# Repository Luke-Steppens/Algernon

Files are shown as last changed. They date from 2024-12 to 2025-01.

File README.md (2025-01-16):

# Micromouse Project - COMP207  

## Overview  
This repository contains all the resources, code, and documentation for my Micromouse project as part of the COMP207 module at Falmouth University (Second Year).  
The goal of the project is to design, build, and program a robot capable of navigating a maze efficiently.  

---

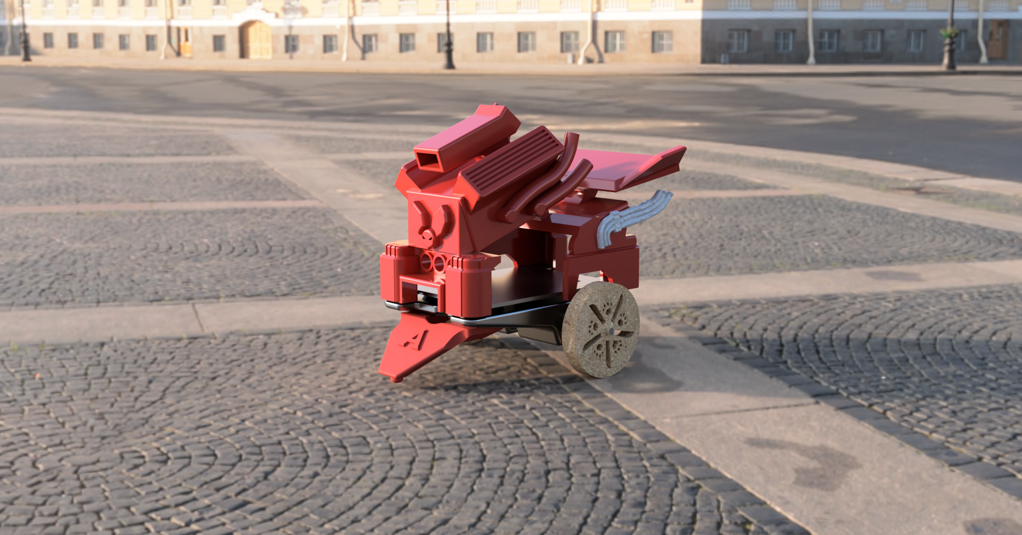
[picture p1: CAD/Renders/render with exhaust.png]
High-Resolution Render


---

## Project Goals  

1. **Design and Manufacture**  
   - Create an autonomous Micromouse capable of navigating a maze.  

2. **Documentation**  
   - Utilise tools such as:  
     - **EasyEDA**: PCB design  
     - **Fusion 360**: 3D modeling  
     - **Arduino IDE**: Programming  

3. **Practical Implementation**  
   - Use physical tools and equipment, including:  
     - 3D printers  
     - Laser cutters  
     - Soldering tools  
     - General workshop tools  

---

## Contest Rules  
For detailed guidelines on Micromouse competitions, refer to the official [Micromouse Classic Contest Rules](https://ukmars.org/contests/contest-rules/micromouse-classic/) provided by UKMARS.  

---

## Development Progress  
Track my project progress through the [COMP207 Micromouse Devlog](https://www.notion.so/COMP207-Digital-Prototyping-Logbook-7b87d9ca3a4f4ccf9538969c8f4991d4?pvs=4).  

---

## Repository Contents  
This repository is organized into the following directories:  

- **CAD**  
   - Assemblies
   - Drawings
   - Parts
   - Renders
   - Workshop Materials  

- **Code**  
   - Basic Component Code  
   - ClassCode  
   - Micro-Mouse Algernon  

- **Documentation**  
   - Screenshots & Photos
   - TCRT Test
   - Feedback Form
   - Notion

- **Electronics**
   - Datasheets

- **Media**
   - Video
   - Photo
   - Presentation - For my presentation please use this link or find the slides in this folder https://www.youtube.com/watch?v=WSdy4DRx-fY&t=1s

---

## How to Recreate the Project  

### 1. **Prepare Initial Components**  

To begin, gather the following components for the Micromouse project:  

<table>
  <tr>
    <td style="text-align: center;">
      <b>Microcontroller:</b><br>Pi Pico<br>
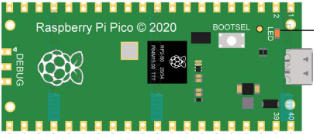
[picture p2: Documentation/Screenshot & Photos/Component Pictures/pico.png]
      
    </td>
    <td style="text-align: center;">
      <b>Motor Driver:</b><br>L293D<br>
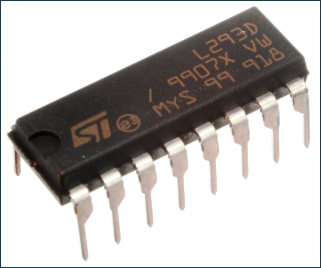
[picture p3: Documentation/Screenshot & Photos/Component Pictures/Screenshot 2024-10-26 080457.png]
      
    </td>
    <td style="text-align: center;">
      <b>Proximity Sensor:</b><br>TCRT5000<br>
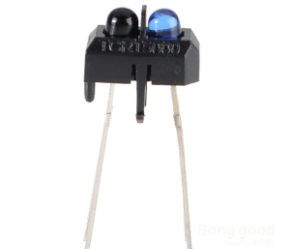
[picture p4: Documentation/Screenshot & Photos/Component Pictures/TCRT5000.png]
      
    </td>
  </tr>
  <tr>
    <td style="text-align: center;">
      <b>Voltage Regulator:</b><br>L7805<br>
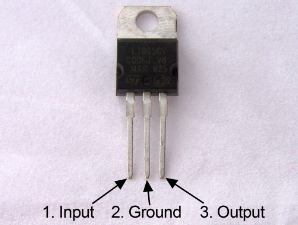
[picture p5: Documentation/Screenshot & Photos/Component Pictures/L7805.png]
      
    </td>
    <td style="text-align: center;">
      <b>Magnetometer Compass:</b><br>GY-271 HMC5883L<br>
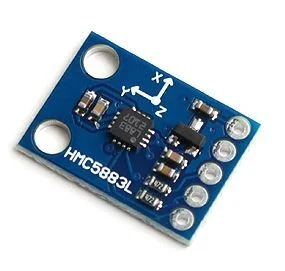
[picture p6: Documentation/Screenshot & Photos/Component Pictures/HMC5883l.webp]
      
    </td>
    <td style="text-align: center;">
      <b>DC Motors:</b><br>12V N20<br>
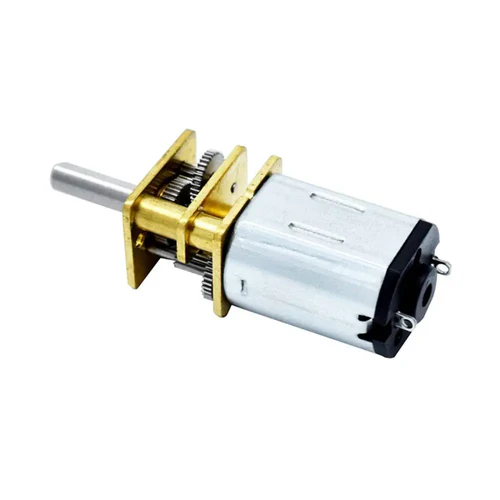
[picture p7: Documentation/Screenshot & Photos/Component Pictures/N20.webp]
      
    </td>
  </tr>
</table>
<br><br> <!-- Extra line break -->

---

### 2. **Schematic Layout - EasyEDA**  

After preparing the components, you can move on to creating the schematic in EasyEDA. This is where you arrange the components logically on the schematic to plan how they’ll be connected.  

It can often be difficult to find the item you are looking for within EasyEDA's search function, so I advise using the "User Contributed" section for additional parts.
This section has a variety of parts that other users have uploaded, which can save you time searching for specific components.

<div style="text-align: center; margin-bottom: 20px;">
  <b>User Contributed Section</b><br>
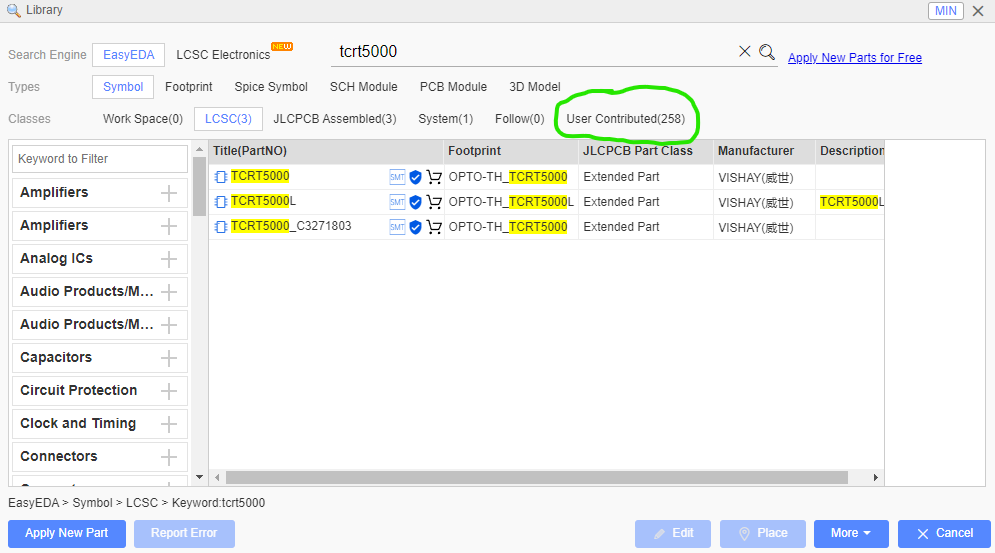
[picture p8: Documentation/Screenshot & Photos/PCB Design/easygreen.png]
  
</div>

### Component and ID’s

Here are the components used in the project along with their EasyEDA search IDs:

- **Pi Pico** - C7203003
- **Motor Driver (L293D)** - C12340
- **Proximity Sensor (TCRT5000)** - C2984661
- **Switch** - C2939728
- **Voltage Regulator (L7805)** - C347289
- **Compass (HMC5883L)** 

Here's an example of how the schematic layout in EasyEDA looks:

<div style="text-align: center; margin-bottom: 20px;">
  <b>EasyEDA Schematic Layout</b><br>
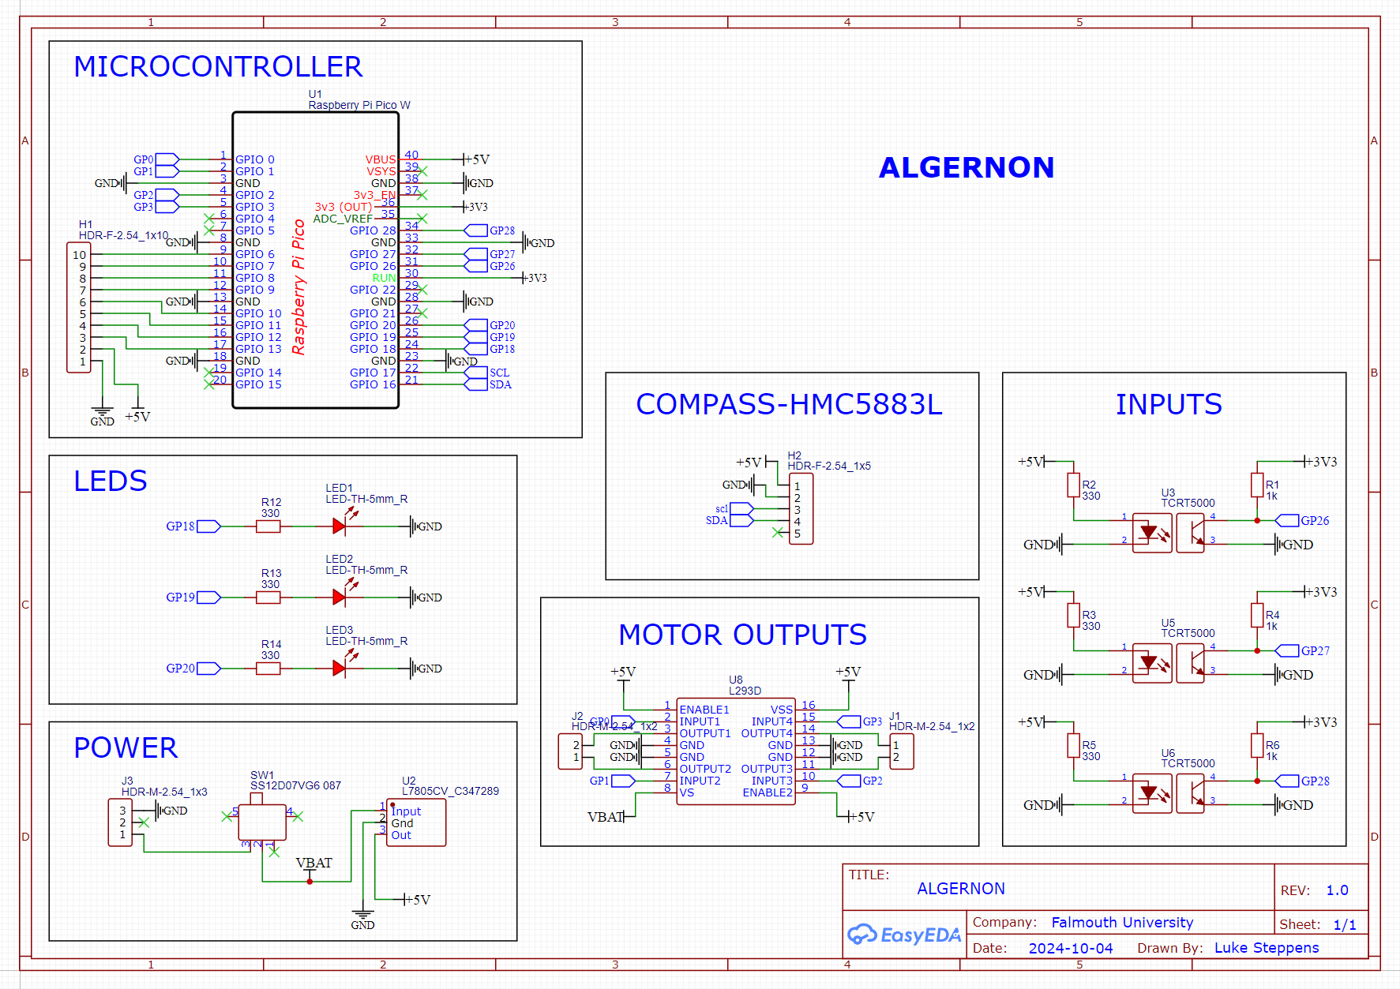
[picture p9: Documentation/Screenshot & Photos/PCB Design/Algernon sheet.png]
  
</div>
Please ensure you check your datasheets to get the connections correct. I took the incorrect details from a sellers page and had troubles down the line. (It is Corrected in this Schematic)

<br><br> <!-- Extra line break -->

---
### 3. **PCB Layout - Fusion 360 / EasyEda**

Design the base shape for your PCB in Fusion 360 by starting with a basic rectangle. Add four circles for mounting the PCB to the motor mounts,
then extrude the shape to a thickness of **1.60mm**. Apply fillets to the corners to create smooth edges. Once the base shape is complete,
create a new sketch on the surface of the design. After finishing the sketch, right-click on it in the drop-down menu and save it as a **DXF file**.

<div style="text-align: center; margin-bottom: 20px;">
  <b>Base Design of PCB</b><br>
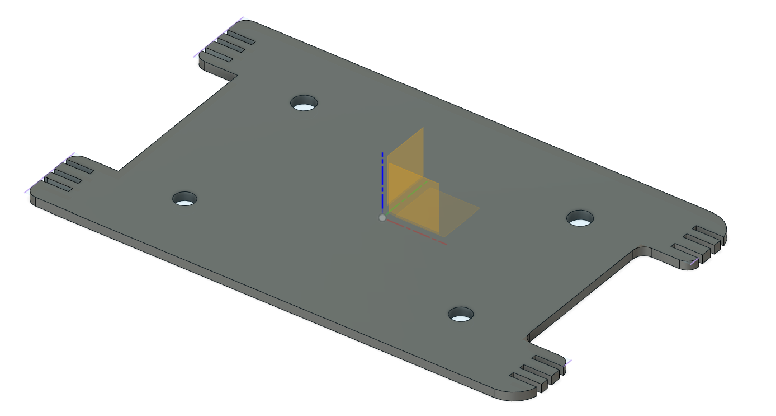
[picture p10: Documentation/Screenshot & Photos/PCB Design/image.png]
  
</div>

<br><br> <!-- Extra line break -->

The next step is to import your DXF file into EasyEDA and place your schematic on it. Consider the placement of components carefully to ensure proper functionality. For instance, the TCRT5000 proximity sensors should be positioned at the edges, and the L7805 voltage regulator is quite tall, so it may interfere with the chassis design. To make the routing process easier, we can utilize both the top and bottom layers of the PCB, represented by the red and blue lines, respectively. Add a copper layer within the PCB that way there is no need to connect ground connections, of which there are many. Alongside this do the same with +5V removing more manual connections and saving time. 
<div style="text-align: center; margin-bottom: 20px;">
  <b>Layout Considering Physicality of Components and Tracks</b><br>
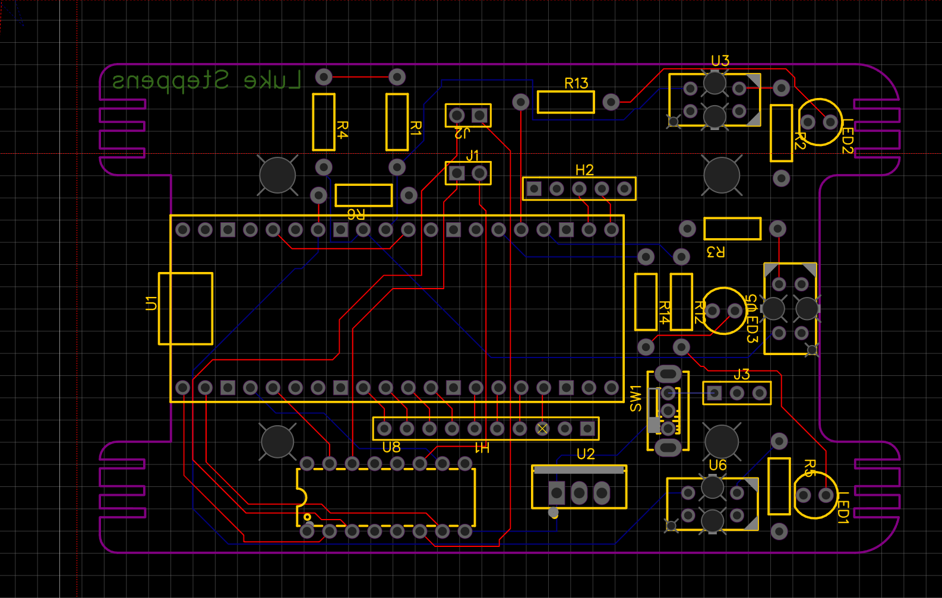
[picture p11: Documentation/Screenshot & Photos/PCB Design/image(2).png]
  
</div>

<br><br> <!-- Extra line break -->

When routing the board, avoid creating arbitrary lines. Instead, aim to have the tracks run parallel to one another. Shorter tracks result in less resistance, improving performance. Next press the Design Rule Check button too see if everything is correct, if you have no errors feel free to proceed.
<div style="text-align: center; margin-bottom: 20px;">
  <b>Final Track Layout</b><br>
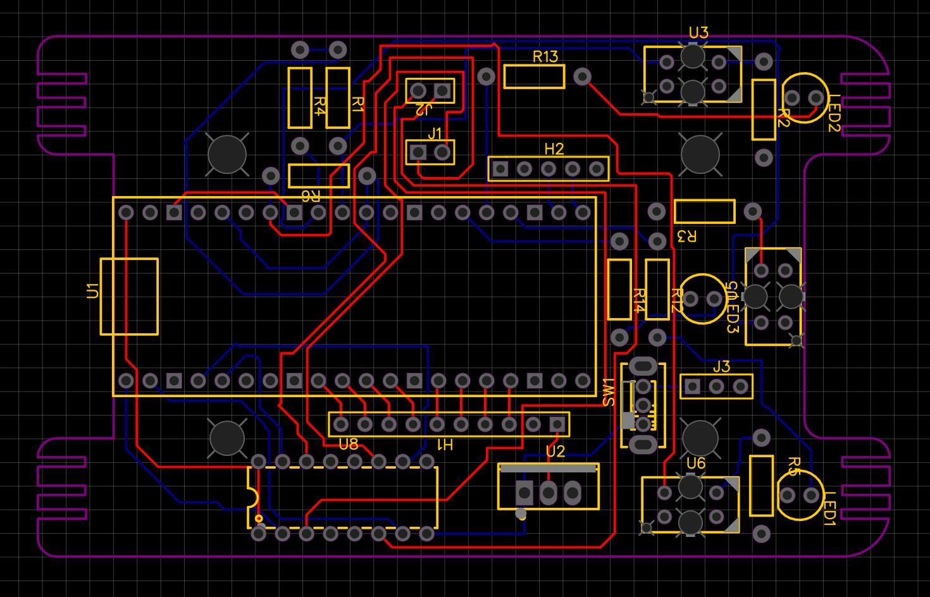
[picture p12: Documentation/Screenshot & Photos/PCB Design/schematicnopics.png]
  
</div>

<br><br> <!-- Extra line break -->

Once you are pleased with your setup press the 3D button to get an idea of the final product.
<div style="text-align: center; margin-bottom: 20px;">
  <b>PCB 3D Render</b><br>
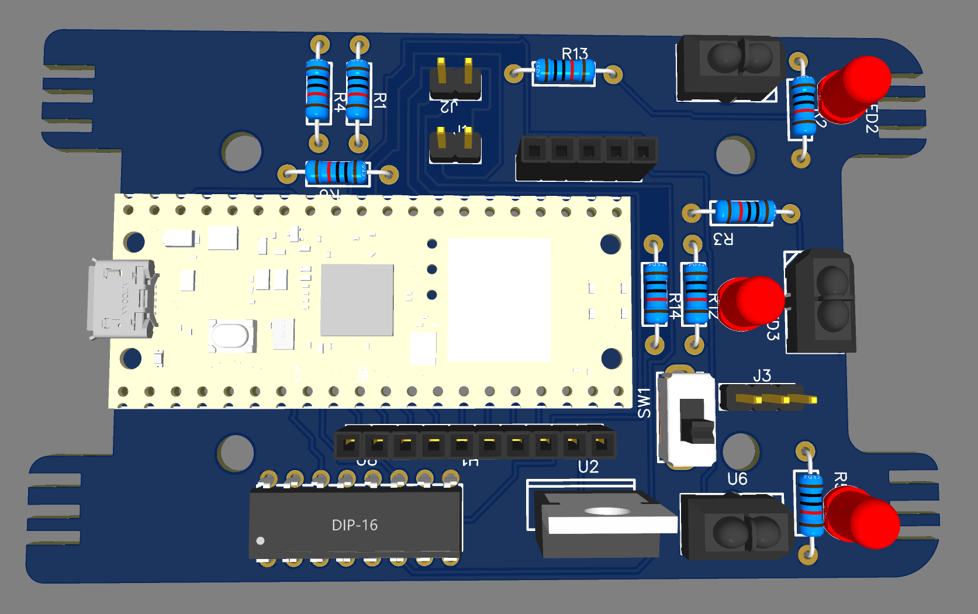
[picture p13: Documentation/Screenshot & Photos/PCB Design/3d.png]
  
</div>

---
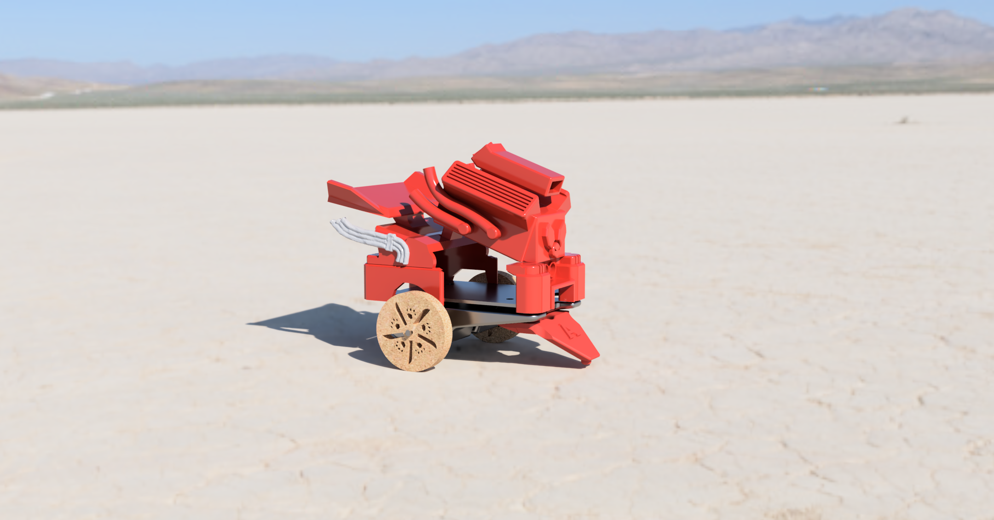
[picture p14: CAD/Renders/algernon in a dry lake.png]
High-Resolution Render


---

<br><br> <!-- Extra line break -->
---
### 4. **Motor Mounts - Fusion 360** 

Firstly a sketch is placed and we begin building a basic block with holes with which to attach the PCB. The centre rectangle was made 90mm by 25mm giving lots of space, and then use the construction line tool to find the spots 25mm away from the centre east and west. These would be the places for the PCB holes, the circle tool was used at 3.60 diameter and then use the offset tool to add another circle 2mm larger around it. Extrude 20mm leaving the two circles deselected which leaves the holes going through the block.

<div style="text-align: center; margin-bottom: 20px;">
  <b>Base Dimensions</b><br>
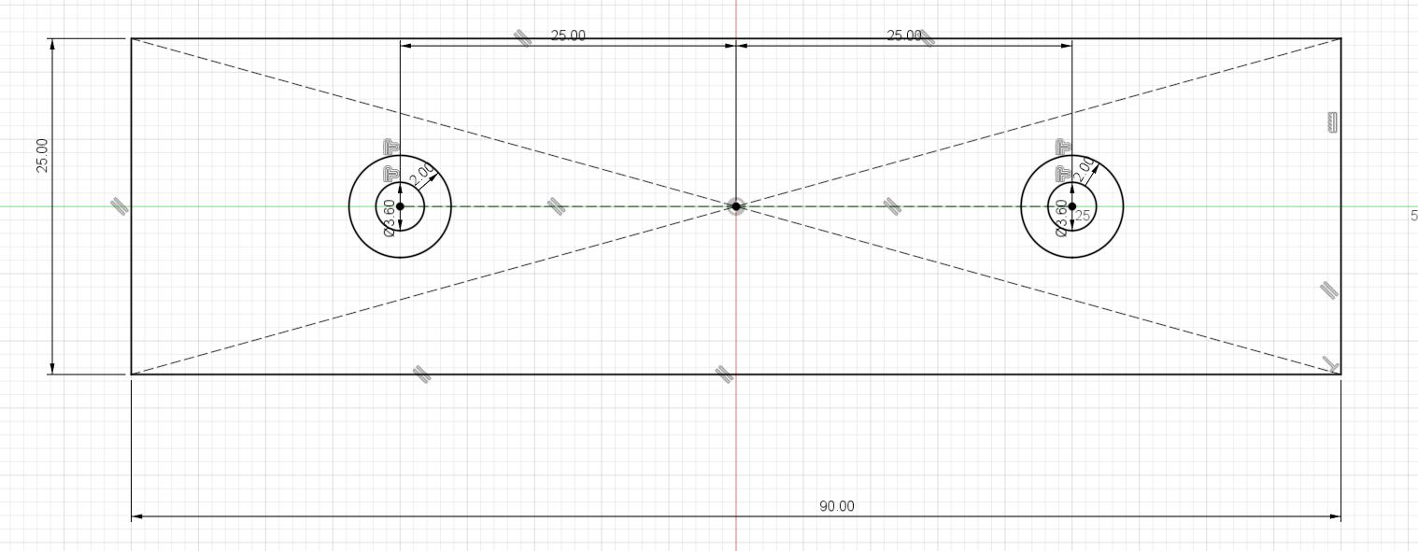
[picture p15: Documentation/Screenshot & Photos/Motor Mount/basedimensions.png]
  
</div>

<div style="text-align: center; margin-bottom: 20px;">
  <b>Base Extrude</b><br>
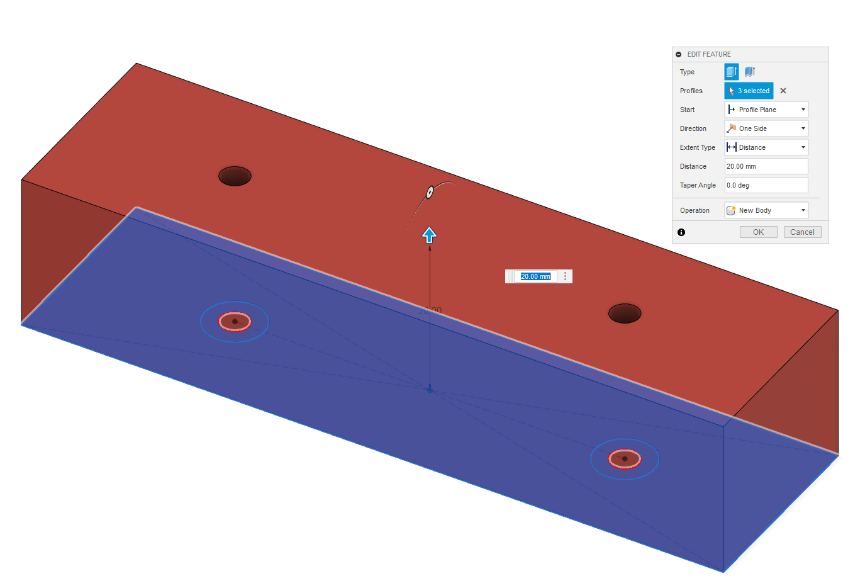
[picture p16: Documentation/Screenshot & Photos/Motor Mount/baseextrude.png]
  
</div>

<br><br> <!-- Extra line break -->

next step is to carve out the hole for the DC motor and to create the shape of the mount itself. Make a sketch on the side and then used the line tool just selecting points then extruding through. The motor hole has to follow the specification of its real life counterpart, sketch a circle of 12mm and a square of 10mm from the circles centre, this leaves the centre part ready for the extrusion process.

<table>
  <tr>
    <td style="text-align: center;">
      <b>Mount Shape</b><br>
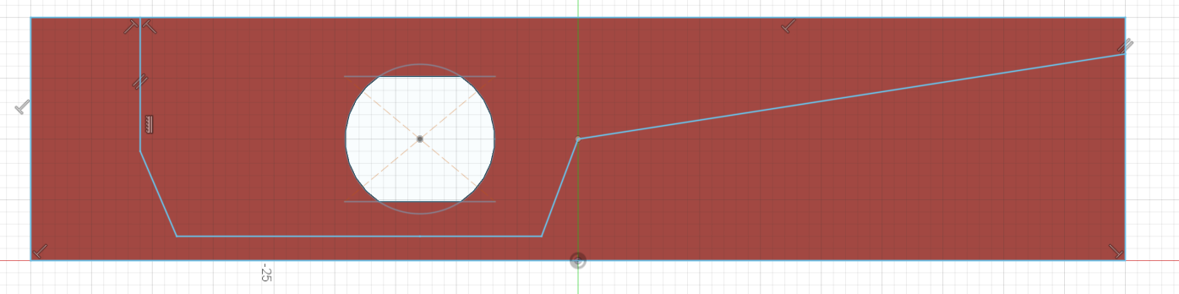
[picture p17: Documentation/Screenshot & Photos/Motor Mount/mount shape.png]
      
    </td>
    <td style="text-align: center;">
      <b>Extrude Cut</b><br>
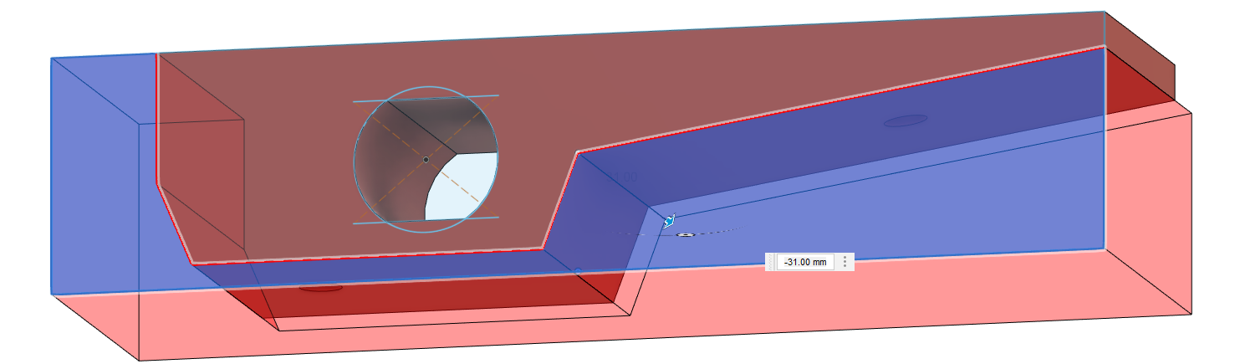
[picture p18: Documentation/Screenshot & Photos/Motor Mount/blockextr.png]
      
    </td>
  </tr>
</table>

<br><br> <!-- Extra line break -->

Between the PCB and mount we need 3mm clearance. extrude the offset circles on the surface to 3mm and then chamfer them down giving a ramped effect. Pure for aesthetics extra edges can be filleted to be smooth and rounded.

<table>
  <tr>
    <td style="text-align: center;">
      <b>Offset Circle Extrude + Offset</b><br>
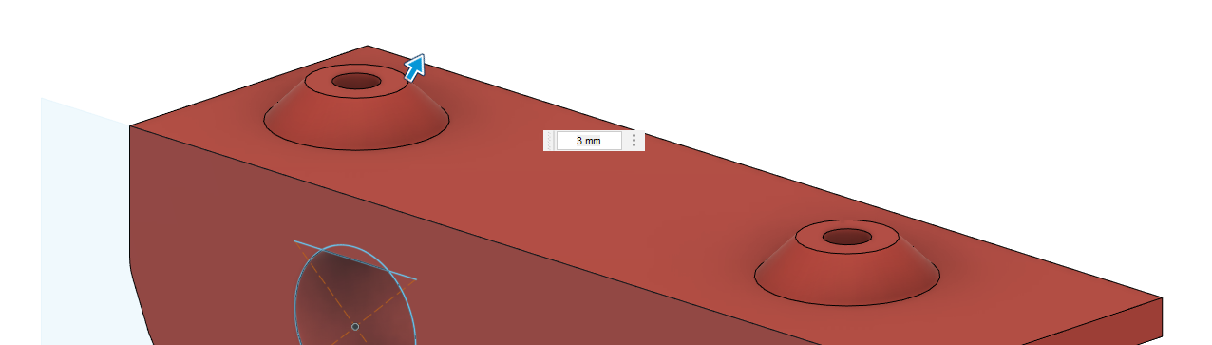
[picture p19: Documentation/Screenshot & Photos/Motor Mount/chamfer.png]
      
    </td>
    <td style="text-align: center;">
      <b>Filleted Edges</b><br>
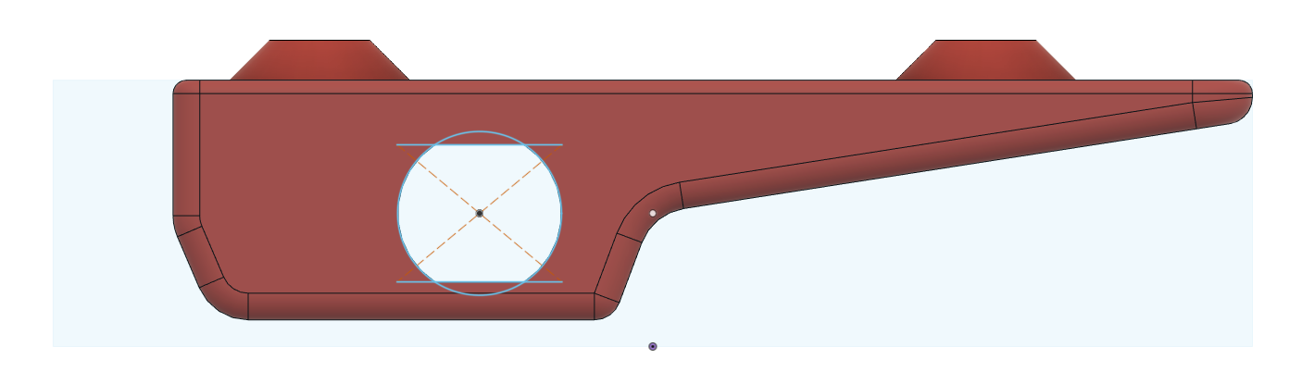
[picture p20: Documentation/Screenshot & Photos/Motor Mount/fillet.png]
      
    </td>
  </tr>
</table>
<br><br> <!-- Extra line break -->

In order to have the mount screws fit correctly a horizontal extrude is needed on the underside. An extrude was made on the side sketch of the mount with and offset creating a square within the middle. Fillet the edge, this will make attaching parts easier later on.

<div style="text-align: center; margin-bottom: 20px;">
  <b>Flat Extrude for Screw Nuts and extras</b><br>
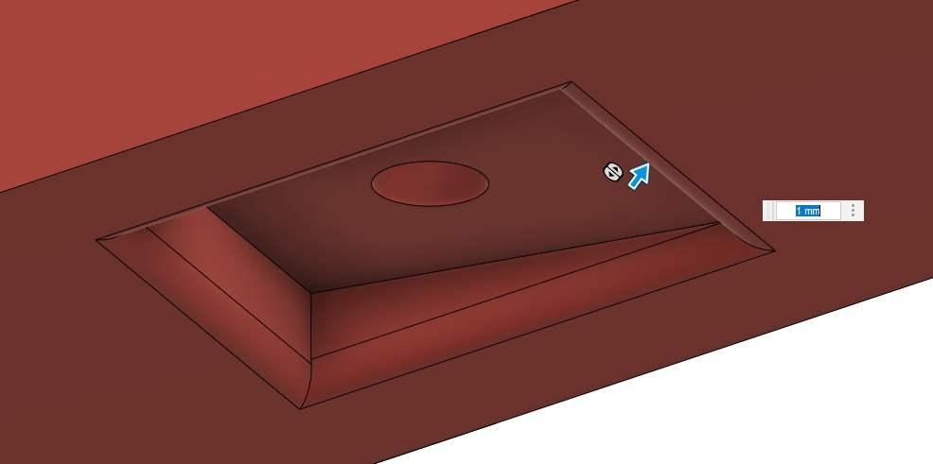
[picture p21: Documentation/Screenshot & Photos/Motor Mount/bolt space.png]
  
</div>

<br><br> <!-- Extra line break -->

For character to make the mounts match the "Paw" shape of the PCB base, cut out 12.5mm by 9mm from the edge by creating a sketch and extruding through.

<table>
  <tr>
    <td style="text-align: center;">
      <b>Paw Shape</b><br>
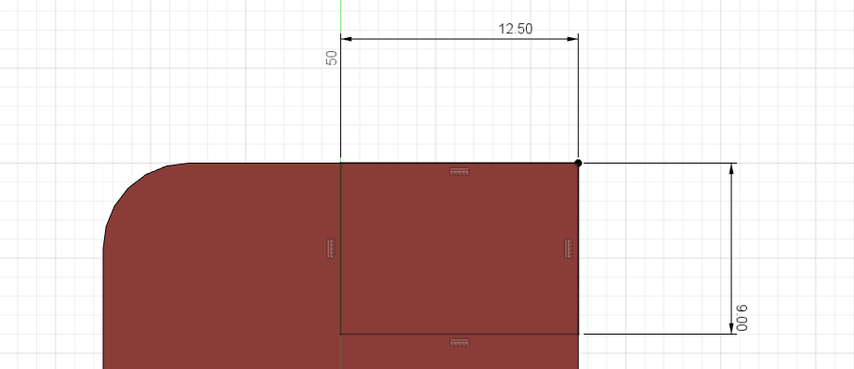
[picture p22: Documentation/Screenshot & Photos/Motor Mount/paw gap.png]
      
    </td>
    <td style="text-align: center;">
      <b>Filleted Edges</b><br>
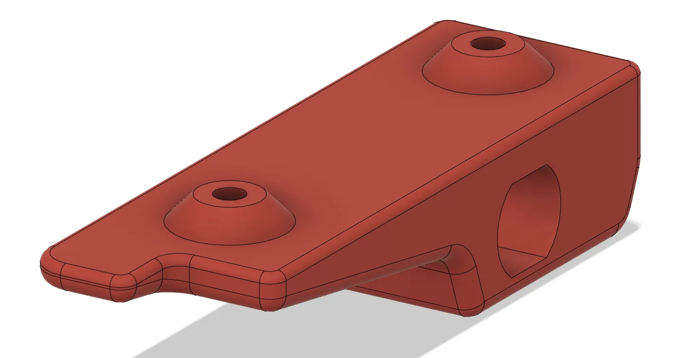
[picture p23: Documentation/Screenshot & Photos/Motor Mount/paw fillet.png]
      
    </td>
  </tr>
</table>

<br><br> <!-- Extra line break -->

To create the motor mounts counterpart create a construction plane that is offset far enough to fit the mirror image. (26mm from the side plane)

<div style="text-align: center; margin-bottom: 20px;">
  <b>Construction Plane</b><br>
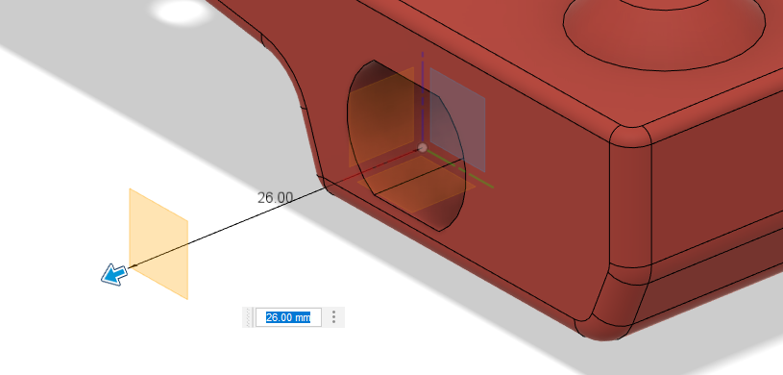
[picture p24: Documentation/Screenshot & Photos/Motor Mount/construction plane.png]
  
</div>

<div style="text-align: center; margin-bottom: 20px;">
  <b>Mirror Mount</b><br>
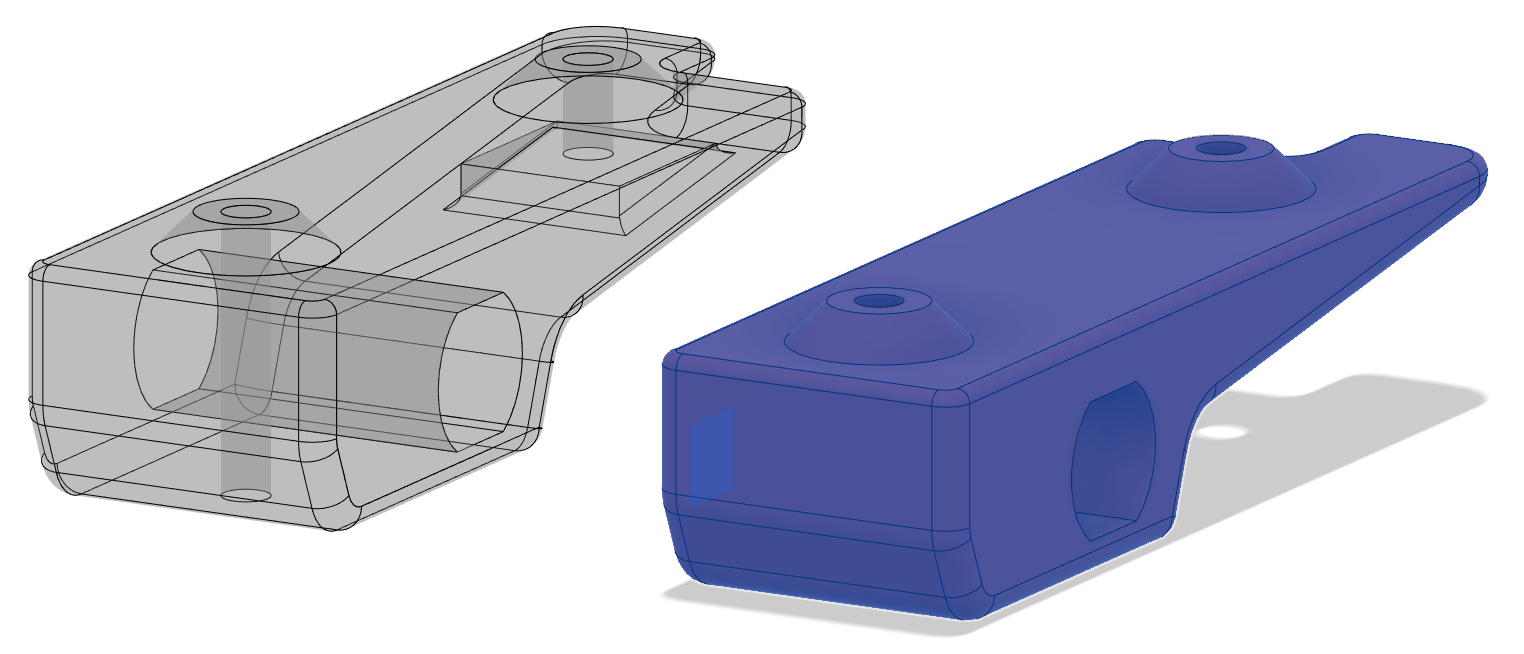
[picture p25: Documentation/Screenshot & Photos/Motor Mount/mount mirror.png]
  
</div>

<br><br> <!-- Extra line break -->

The last touch on the mounts was to add text to the them. Create sketches on the flat surfaces, choose text and type the writing. Follow this with using the alignment option to have the text centered within box. Extrude the Text by 1mm.

<table>
  <tr>
    <td style="text-align: center;">
      <b>How's My</b><br>
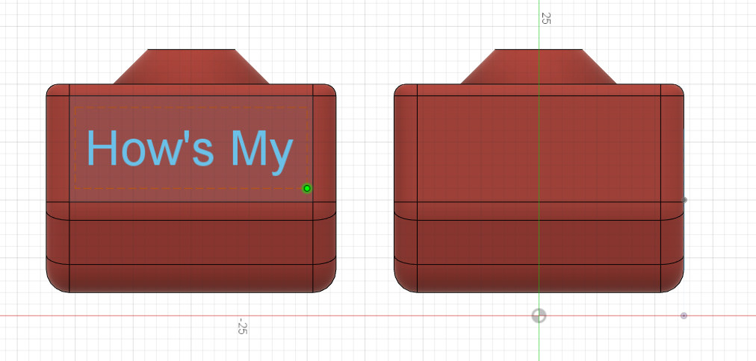
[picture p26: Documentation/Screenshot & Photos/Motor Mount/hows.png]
      
    </td>
    <td style="text-align: center;">
      <b>Driving</b><br>
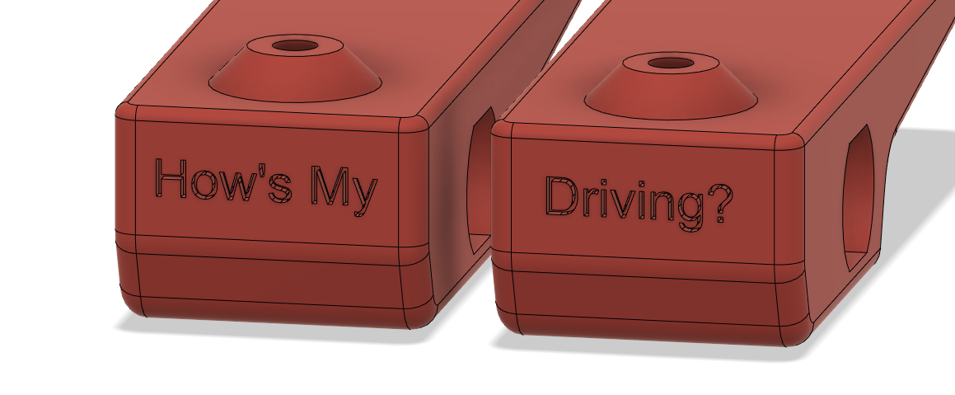
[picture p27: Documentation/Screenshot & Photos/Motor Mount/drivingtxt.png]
      
    </td>
  </tr>
</table>

<br><br> <!-- Extra line break -->

Going back into Fusion 360 you can create an assembly with all current parts which should look like this:

<div style="text-align: center; margin-bottom: 20px;">
  <b>Motor Mount + PCB Assembly </b><br>
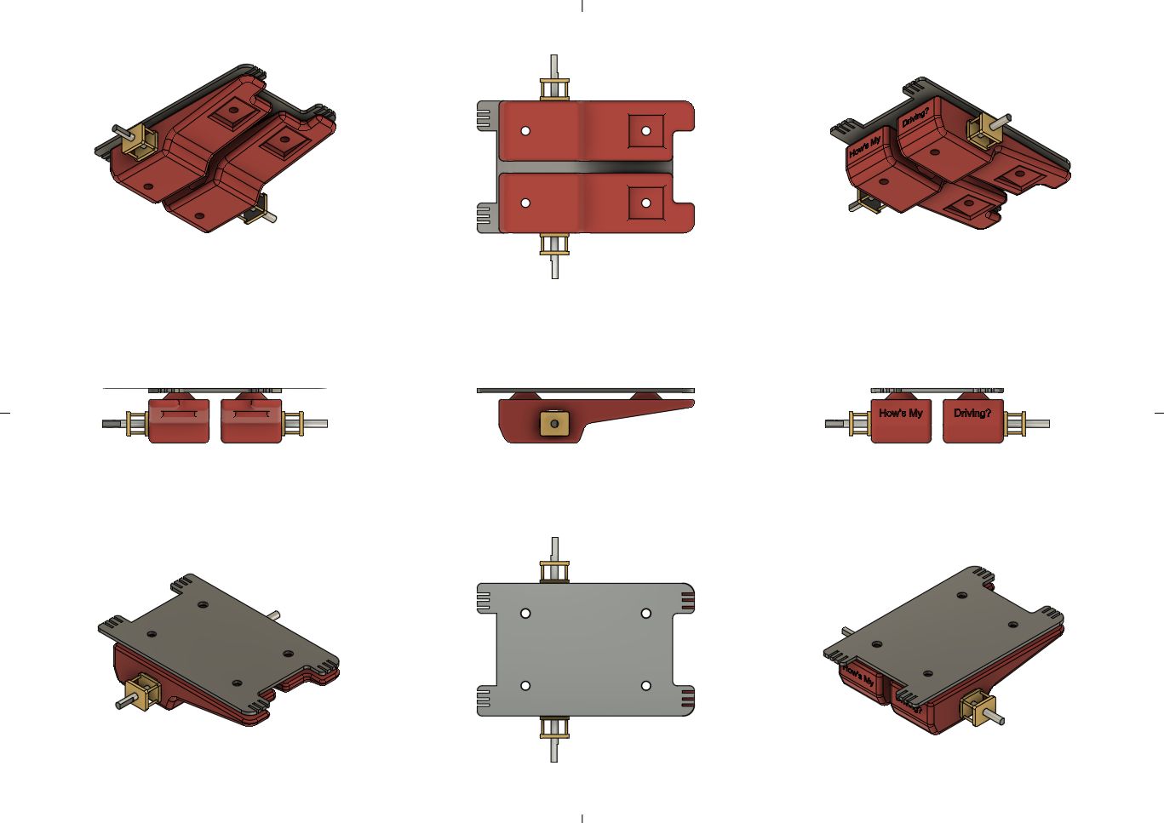
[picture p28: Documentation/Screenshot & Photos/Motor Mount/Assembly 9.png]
  
</div>

<br><br> <!-- Extra line break -->

---
### 5. **PCB Assembly & Testing - Arduino IDE**

Your PCB will need a visual inspection to ensure everything looks connected properly. Then using a multimeter go through each track end to end and connect the multimeter to the end of each tracks, if it doesnt beep they arent connected and it is ok to continue. Check every track!. 

<div style="text-align: center; margin-bottom: 20px;">
  <b>Printed Circuit Board</b><br>
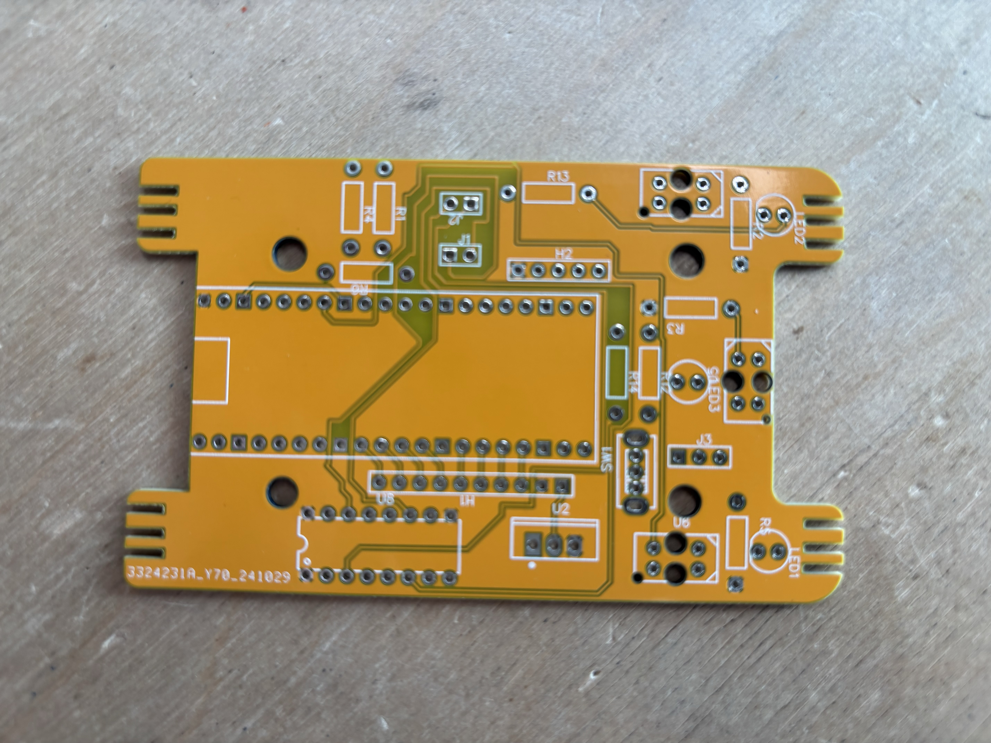
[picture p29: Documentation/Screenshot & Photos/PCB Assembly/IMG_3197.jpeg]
  
</div>

<br><br> <!-- Extra line break -->

Next start attaching and testing components, first is the Pi Pico and once soldered onto the PCB (Ensure the correct side is up, the same as on your EasyEda design) test the onboard LED. To do this you will need to upload the code from Arduino IDE. Tested on a power supply I gave it just over 7 volts and the LED flashed consistently.

```cpp
void setup() {
  pinMode(LED_BUILTIN, OUTPUT);
}

void loop() {
  digitalWrite(LED_BUILTIN, HIGH);
  delay(200);
  digitalWrite(LED_BUILTIN, LOW);
  delay(200);
}
```
<br><br> <!-- Extra line break -->

The next item to solder was the TCRT5000's, make sure to check your schematics before soldering to make sure they are in the correct orientation. Also the LED's can be loose within the TCRT5000's so be extra careful. Onto the soldering the resistors again check your schematics to ensure the placement like below.

<table>
  <tr>
    <td style="text-align: center;">
      <b>Inputs</b><br>
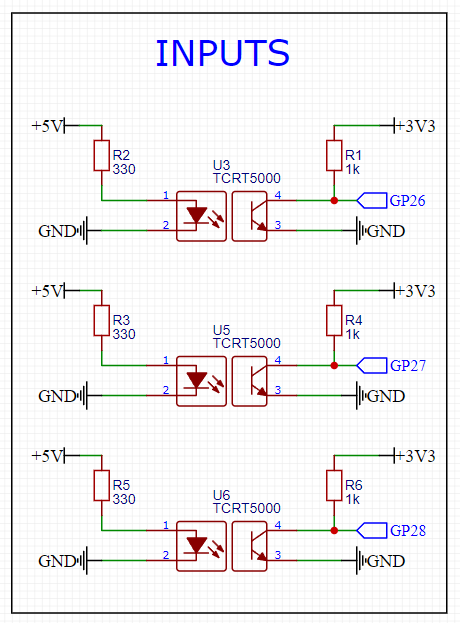
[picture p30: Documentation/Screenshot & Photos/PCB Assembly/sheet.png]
      
    </td>
    <td style="text-align: center;">
      <b>Resistors</b><br>
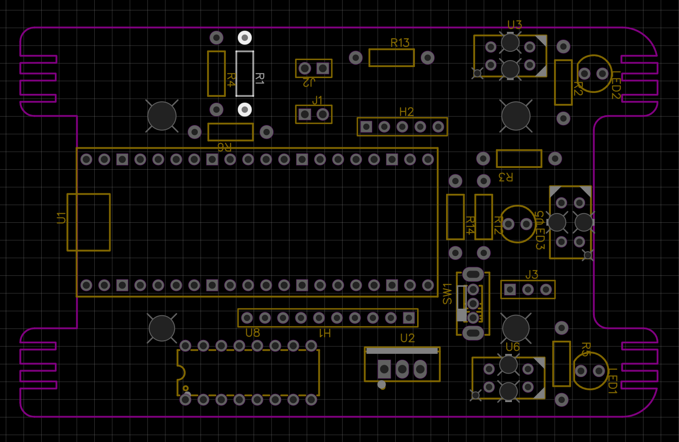
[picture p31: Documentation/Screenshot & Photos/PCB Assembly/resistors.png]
      
    </td>
  </tr>
</table>

Once completed, use the following code snippets to test the LEDs and TCRT5000 sensors. Measuring the centimeter readings from the TCRT5000s using the serial monitor in the Arduino IDE will be valuable for coding navigation. I recommend doing this as early as possible.

```cpp
int TCRT_Left = 26;
int TCRT_Center = 27;
int TCRT_Right = 28;
int TCRT_Output;

void setup() {

  Serial.begin(9600);
  pinMode(TCRT_Left, INPUT);
  pinMode(TCRT_Center, INPUT);
  pinMode(TCRT_Right, INPUT);
}

// gets reading from TCRT on the right and outputs to serial monitor
void loop() {
  TCRT_Output = analogRead(TCRT_Right);
  Serial.print("Right Reading ");  
  Serial.println(TCRT_Output);
  delay(500);
}
```
<br><br> <!-- Extra line break -->

<table>
  <tr>
    <td style="text-align: center;">
      <b>Right TCRT5000</b><br>
      
    </td>
    <td style="text-align: center;">
      <b>LEFT TCRT5000</b><br>
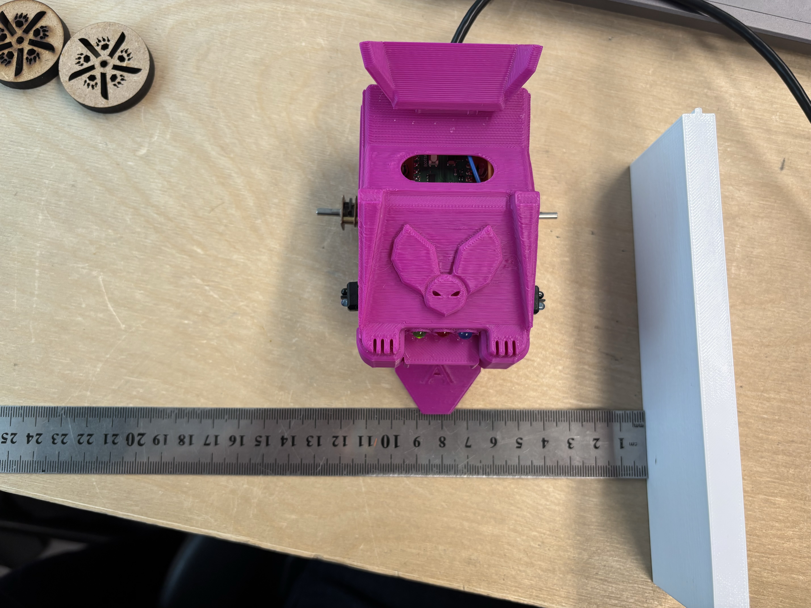
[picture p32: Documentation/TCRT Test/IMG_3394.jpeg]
      
    </td>
  </tr>
</table>

<br><br> <!-- Extra line break -->

Testing the TCRT5000 sensors was based on the 17cm width of the maze corridors. Measurements were taken at 1 cm distances, with results recorded for each up to 8cm approximately half the width of the corridor. Note that each TCRT5000 sensor may produce slightly different results. External factors, such as the reflectivity of the maze wall surface and surrounding light sources, can affect the readings. Aim to replicate conditions similar to those of the maze environment. As you will see in the table below the sensors tend to plateau at higher distances and are more sensitive at closer.

| Distance (CM) | Right TCRT (Range) | Left TCRT (Range) |  Center TCRT (Range) |
|:---:|:---:|:---:|:---:|
| 1 | 543 - 548 | 567 - 569 | 691 - 700 |
| 2 | 851 - 858 | 869 - 876 | 892 - 898 |
| 3 | 940 - 948 | 950 - 959 | 953 - 964 |
| 4 | 974 - 986 | 980 - 990 | 981 - 990 |
| 5 | 993 - 1002 | 995 - 1005 | 994 - 1003 |
| 6 | 1002 - 1023 | 1003 - 1013 | 1001 - 1011 |
| 7 | 1007 - 1015 | 1010 - 1018 | 1007 - 1015 |
| 8 | 1008 - 1018 | 1013 - 1021 | 1007 - 1019 |

<br><br> <!-- Extra line break -->

---
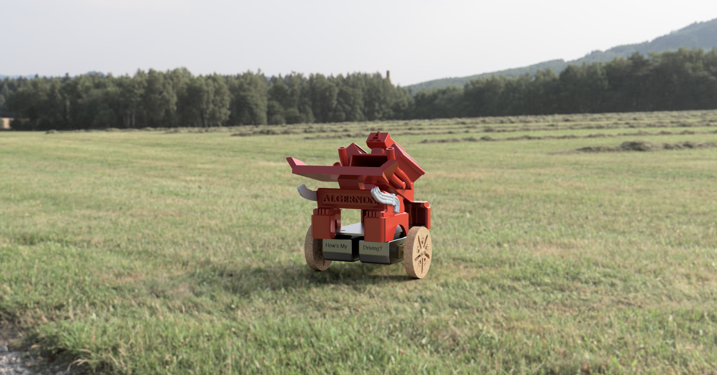
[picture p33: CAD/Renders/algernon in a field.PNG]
High-Resolution Render


---
### 6. **Chassis Design - Fusion 360**

This section will go over the basic construction of a chassis for the micro-mouse. My design is over engineered and over complicated to a fault (But was good practice) you will find my fusion design file is you wish to use it in the Fusion section of the repo.

The initial steps for a basic chassis would be to take your PCB base design and use it as a template. From here create a sketch upon the PCB design and extrude to 5mm, and then create a sketch on the side and using the line tool draw the shape you would like and extrude through. To save time hollowing out the chassis piece by piece just use the shell command and choose a thickness of minimum of 2mm.

<table>
  <tr>
    <td style="text-align: center;">
      <b>Basic Shape</b><br>
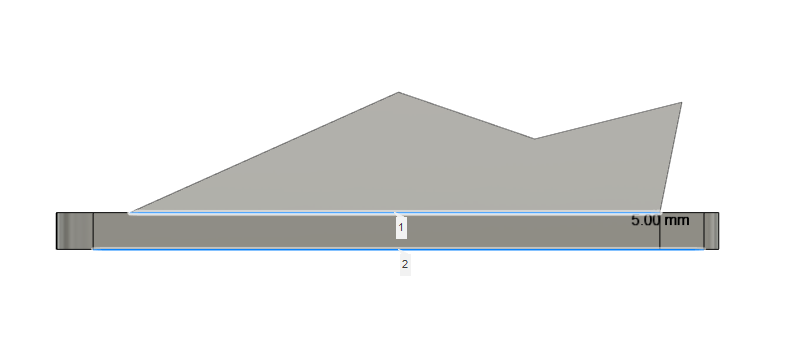
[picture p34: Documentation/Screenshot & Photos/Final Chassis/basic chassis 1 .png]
      
    </td>
    <td style="text-align: center;">
      <b>Shell</b><br>
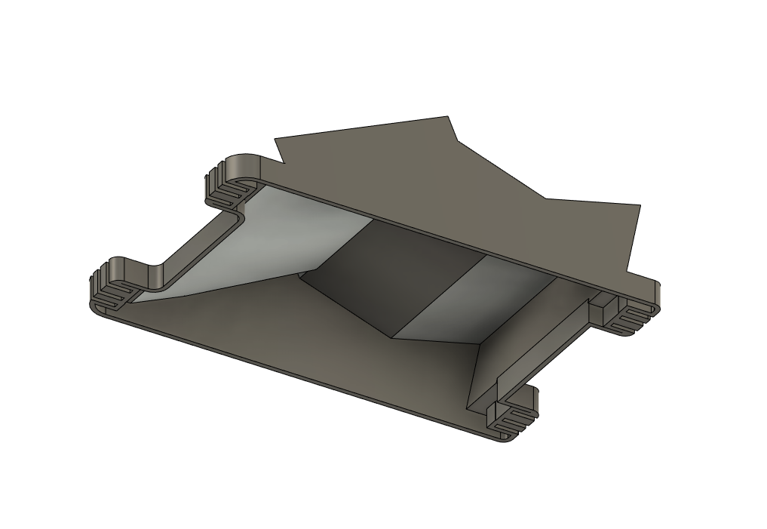
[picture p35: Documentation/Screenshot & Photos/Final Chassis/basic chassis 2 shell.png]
      
    </td>
  </tr>
</table>

<br><br> <!-- Extra line break -->

Because the TCRT5000's have to be postitioned center, left and right we need to make sure there is a place for them so we extrude to cut a gap for them. Again this is done by creating a side sketch and extruding after drawing with the line tool. For a bit of fun you can create a design on the bonnets face, I did this by drawing with circle and line tools on the face and then using the mirror function so I could ensure symmetry. To use the mirror fucntion pick the the design (so far) and then pick the mirror plane going horizonally through the chasses perpendicular to the design. 

<table>
  <tr>
    <td style="text-align: center;">
      <b>Basic Shape</b><br>
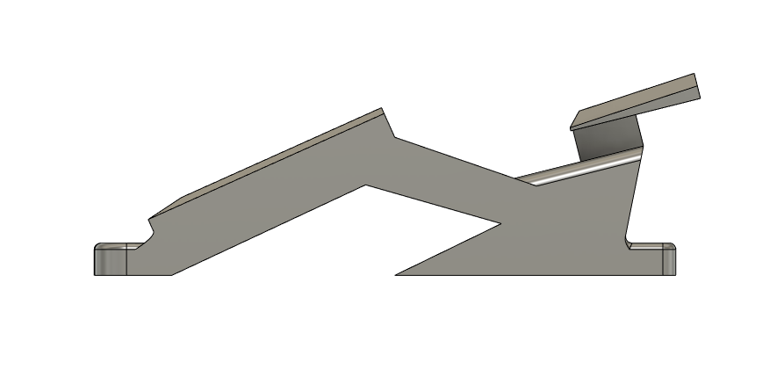
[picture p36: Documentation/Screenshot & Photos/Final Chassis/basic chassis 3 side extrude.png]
      
    </td>
    <td style="text-align: center;">
      <b>Shell</b><br>
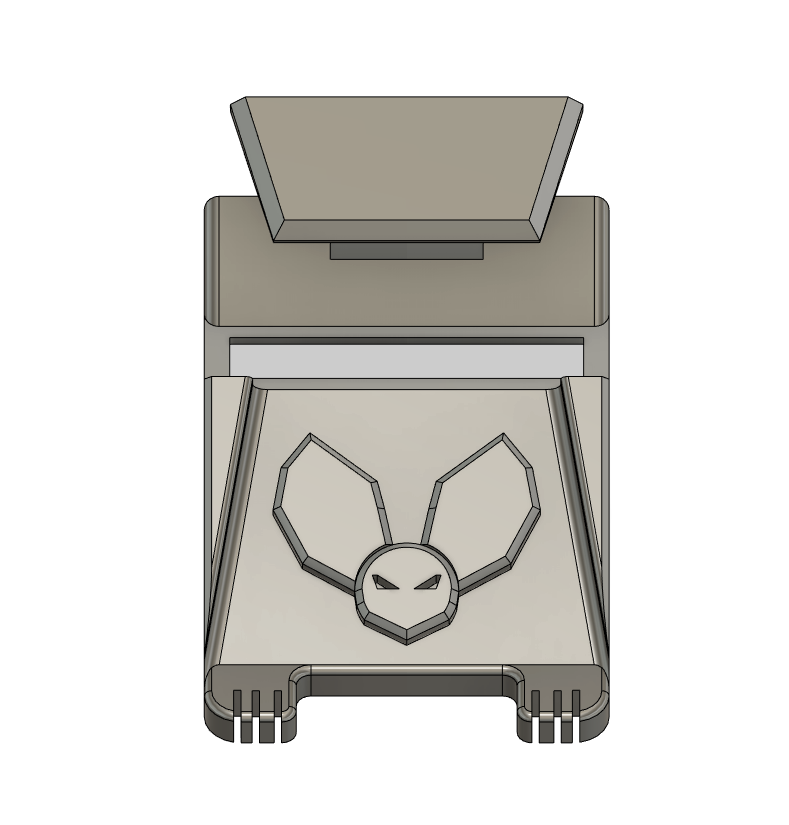
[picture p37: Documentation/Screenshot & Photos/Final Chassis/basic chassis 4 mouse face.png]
      
    </td>
  </tr>
</table>

<br><br> <!-- Extra line break -->

At this point your chassis has the same curcumference measuraments as the PCB and so wont fit over it, alongside this there is currently not enough clearance for the volatage regulator. So first create a sketch on the underside outer base and use the offset tool and increase this by 2mm. then extrude this by enough 8mm (This will increase to 17mm with later modification). When raised enough make a 2mm thickness extrusion between the paws and draw three 5mm holes for the LED's and extrude them through. Below the LED's a simple three rectangles are drawn and extruded out 15mm, this serves to stop light from the LED's interfereing with the front TCRT5000.

<table>
  <tr>
    <td style="text-align: center;">
      <b>Offset and Lift</b><br>
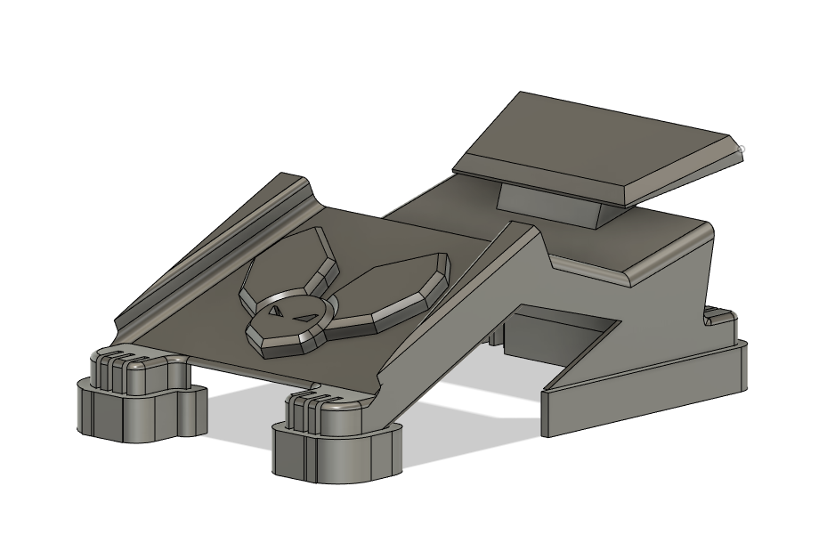
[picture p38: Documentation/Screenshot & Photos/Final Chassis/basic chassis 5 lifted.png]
      
    </td>
    <td style="text-align: center;">
      <b>LED's + Center TCRT5000</b><br>
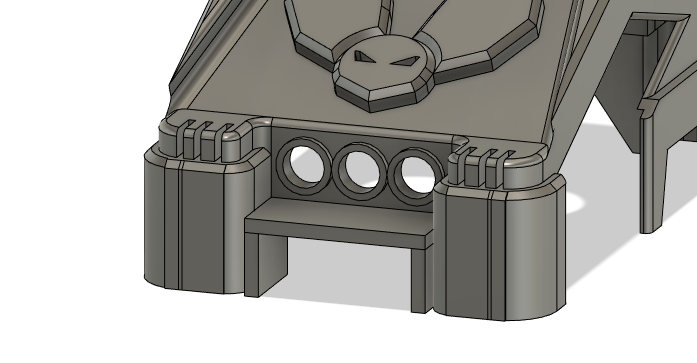
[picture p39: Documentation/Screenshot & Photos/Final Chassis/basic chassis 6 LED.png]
      
    </td>
  </tr>
</table>

<br><br> <!-- Extra line break -->

From here we extend the length of the chassis by using the Split Body feature. Seperate by 10mm and then on the cut surface extrude to meet the face of the other side. This has to be done to give more clearance along the chassis otherwise it takes to much force to attach it to the PCB. 

<table>
  <tr>
    <td style="text-align: center;">
      <b>Split Body</b><br>
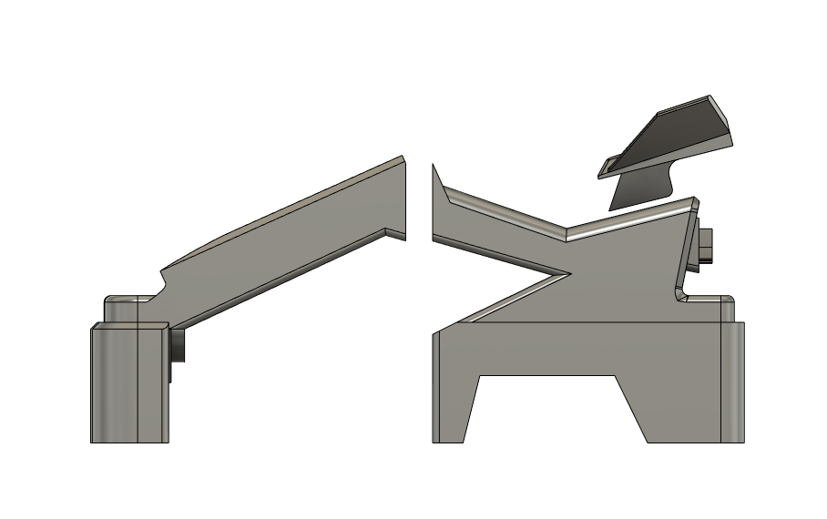
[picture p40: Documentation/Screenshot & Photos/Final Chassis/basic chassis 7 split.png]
      
    </td>     
  </tr>
</table>

<br><br> <!-- Extra line break -->

The final Chassis is a heavily modified version of the above design. The chassis needs a place to hold the battery and so we will design the holder and then use the combine function to add it to the main chassis body. This design also gets heavily modified purely for aesthetics and is already made in the final chassis fusion file.

<table>
  <tr>
    <td style="text-align: center;">
      <b>Battery Holder Measurements</b><br>
      
    </td>
    <td style="text-align: center;">
      <b>Battery Holder</b><br>
      
    </td>
  </tr>
</table>

<br><br> <!-- Extra line break -->
Final Battery Holder Design

<table>
  <tr>
    <td style="text-align: center;">
      <b>Battery Holder Front</b>
      
    </td>
    <td style="text-align: center;">
      <b>Battery Holder Side</b>
      
    </td>
    <td style="text-align: center;">
      <b>Battery Holder Back</b>
      
    </td>
  </tr>
  <tr>
    <td style="text-align: center;">
      <b>Battery Holder Top</b>
      
    </td>
    <td style="text-align: center;">
      <b>Battery Holder Angle</b>
      
    </td>    
  </tr>
</table>

<br><br> <!-- Extra line break -->

This battery holder is then attached via the combine function and parts were extruded away to leave more space but these are also options leaving the final chassis.

<table>
  <tr>
    <td style="text-align: center;">
      <b>Final Chassis Front</b>
      
    </td>
    <td style="text-align: center;">
      <b>Final Chassis Side</b>
      
    </td>
    <td style="text-align: center;">
      <b>Final Chassis Back</b>
      
    </td>
  </tr>
  <tr>
    <td style="text-align: center;">
      <b>Final Chassis Top</b>
      
    </td>
    <td style="text-align: center;">
      <b>Final Chassis Angle</b>
      
    </td>    
  </tr>
</table>
<br><br> <!-- Extra line break -->

---
### 7. **Wheel Design - Fusion 360**

For the wheel the bigger the diameter the faster the mouse will go. Create a new sketch on a flat surface and use the circle fucntion to create a circle 38mm in diameter, 
then create another inner circle of 3mm and from its center make a vertical construction line of 1mm. Now create a horizontal line cutting through the circle purpendicular to the construction line. Then using the snipping tool cut away all excess lines and you will be left with the shape of the motor shaft.

<table>
  <tr>
    <td style="text-align: center;">
      <b>Wheel Diameter</b><br>
      
    </td>
    <td style="text-align: center;">
      <b>Motor Shaft Shape</b><br>
      
    </td>
  </tr>
</table>

(After fitting this style wheel I found the mouses overall width to be to large so I went on to use the 3mm circle without the cut, this allowed the wheels to be closer to the body of the mouse)

<br><br> <!-- Extra line break -->

Next create a new sketch and using basic shapes create a crude paw shape. Once this is made extrude the wheel shape to 6mm. In the create drop down choose pattern and then circular, now chose all the lines that make up the paw shape and then choose the center of the wheel for the pattern to rotate around.

<table>
  <tr>
    <td style="text-align: center;">
      <b>Paw Design</b><br>
      
    </td>
    <td style="text-align: center;">
      <b>Extrude</b><br>
      
    </td>
  </tr>
</table>

<br><br> <!-- Extra line break -->

For the last part of the design I followed the previous steps and created a circular pattern of rectangles, extruded them through (like inverted spokes) and then filleted edges to give a directional effect. 

<table>
  <tr>
    <td style="text-align: center;">
      <b>Spokes Design</b><br>
      
    </td>
    <td style="text-align: center;">
      <b>Final Wheel</b><br>
      
    </td>
  </tr>
</table>

With this ready the next step is to create a sketch on the surface of the wheel and export it as a DXF file and then use 6mm MDF and have the design laser cut. Using a simple glue gun apply enough to secure each wheel.

<br><br> <!-- Extra line break -->

---
### 8. **3rd Point Balance - Fusion 360**

One of the last things the mouse needs is a point of balance at the front. There are three points of balance the two wheels and a small point that with make contact with the ground. In fusion 360 we need to take the measurements from the motor mounts above and create two basic squares the correct distance apart, then create 3mm holes and extrude the shapes. Fillet the top edges of the squares for an easy fit. Now with the line tool draw an arch shape and extrude downward, from here make a sketch on the side and draw a triangle on the side you want to be the back and then extrude cut through both. This should leave you with the second picture.

<table>
  <tr>
    <td style="text-align: center;">
      <b>Connecting Faces</b><br>
      
    </td>
    <td style="text-align: center;">
      <b>Angle Extrude</b><br>
      
    </td>
  </tr>
</table>

<br><br> <!-- Extra line break -->

Using the face shapes extrude out to give enough length for clearance (this will be changed later).
Next create another side sketch and with the line tool make a downward slope to 5mm away from where the ground will be. Cut through with various extrudes until you get the shape you want and then create a 5mm diameter circle and extrude it out 5mm.

<table>
  <tr>
    <td style="text-align: center;">
      <b>Legs Extrude</b><br>
      
    </td>
    <td style="text-align: center;">
      <b>Slope + Point</b><br>
      
    </td>
  </tr>
</table>

<br><br> <!-- Extra line break -->

This is the final shape so feel free to chamfer and fillet edges for a nice look. The two legs leading to the 3rd point are too long so to shorten them first we need touse the split body function, with them now in to parts extrude the legs to a suitable length and then move both bodies together and use the combine function to make them a singular body.

<table>
  <tr>
    <td style="text-align: center;">
      <b>Chamfer + Fillet</b><br>
      
    </td>
    <td style="text-align: center;">
      <b>Split Body</b><br>
      
       </td>
    <td style="text-align: center;">
      <b>Combine</b><br>
      
    </td>
  </tr>
</table>

<br><br> <!-- Extra line break -->

Another optional extra is to add the text A, to do this simply create a sketch on the surface use the text function. Choose your font, size and positioning. This should leave you with the balance ready to attach to the motor mounts.

<table>
  <tr>
    <td style="text-align: center;">
      <b>Text View</b><br>
      
    </td>
    <td style="text-align: center;">
      <b>Side View</b><br>
      
    </td>
  </tr>
  <tr>
    <td style="text-align: center;">
      <b>Angle View</b><br>
      
    </td>
    <td style="text-align: center;">
      <b>3rd Point Balance + Motor Mounts</b><br>
      
    </td>
  </tr>
</table>

<br><br> <!-- Extra line break -->

---
### 9. **Twin Exhaust - 3D Scanning / Fusion 360**

The last physical addition to the micro mouse uses a 3D scanning technique on a phone app called Polycam. The shape for the exhaust was made out of clay and then scanned with the Polycam application. For best results take as many photos as it allows to get greater quality. The file you download is a GLTF which needs to be converted into an STL file.

<table>
  <tr>
    <td style="text-align: center;">
      <b>Exhaust Mesh</b><br>
      
    </td>
    <td style="text-align: center;">
      <b>Dual Exhaust Meshes</b><br>
      

  </tr>
</table>

<br><br> <!-- Extra line break -->

Once imported into fusion a few steps must be taken in order to make this shape 3D printable. First off Using the construction plane tool place a plane below the object and extrude to add a body to meet the bottom of the 3D scan, this effectively make it one solid piece than can be manipulated easier. Next cut around the object using the spline tool and then extrude chunks of the picture away. Fusion seemed to fail when attempting to extrude everything away in one go, so this may take some tinkering. Finally Mirror the exhaust and you are ready to 3D print the exhausts. Within orcaslicer you may have to change the scale to a reasonable size. Once printed attach the exhausts to both side using a glue gun and the final product should look like the picture below.

<br><br> <!-- Extra line break -->

---

High-Resolution Render

<br><br> <!-- Extra line break -->

---
### 10. **Feedback (Market Testing) - Microsoft Word**

<br><br> <!-- Extra line break -->

Feeback

| **Participant Name** | **Participant 1** | **Participant 2** | **Participant 3** |
|---|---|---|---|
| | Charlie | Conor | Ana |
| **If a specific area could use more attention, what would it be and why?** | 9/10<br>The front, there’s a design difference in the LEDs used but other than that it looks grand. | 7/10<br>The wires don’t jut out of the board which is nice but the extra greblies and aesthetics need to be scaled to probably reduce weight and height. | 8/10<br>For future PCB redesigns the motor pins and switch could be moved to a more convenient place on the board. The Fusion 360 could use less attention; anything past the current 3D print state would be slight overkill. |
| **Does the mouse cover all desired requirements to a decent degree?** | 9/10<br>It looks amazing and the code is documented very well. I’m not sure if it can solve the maze at this point. | 9/10<br>The micro mouse moves through the maze quite well and the coding is greatly structured and clearly commented but I think the spoil might be much and might catch on turns. | 6/10<br>The code could use some work as in the currently the mouse spins no matter the TCRT input. |
| **Which component could have a better placement to make the user experience better?** | 8/10<br>The switch could be in a more convenient place for the user | 8/10<br>The position of the battery could be switched to the bottom of the robot and the TCRT’s on the side should be angled more towards the front due to cone of vision. The placement of the other components is nice. | 7/10<br>The switch and the voltage regulator can be swapped around for ease of access. The resistors also seem to be arbitrarily placed on the PCB. |

Addressing feedback

Question 1. For the first question the responses go over placement of components and the over engineering of the design. These are both valid criticisms. Going forward creating simpler designs will allow for less trouble when unforeseen problems occur, having the components better placed will also work well towards keeping things simple, helping the iterative process.

<br><br> <!-- Extra line break -->

Question 2. The code is the focus of the feedback for this question. While the TCRT5000's can be a little unpredictable, I have been made aware of ideas that may help that I would like to implement if there is enough time. The main thing would be having the sensors take readings on startup and use those measurements to base the movements upon. Currently they are set to fixed numbers which aren’t always true when it comes to the sensors, this can be due to natural light and shadows.

<br><br> <!-- Extra line break -->

Question 3. The main point of this piece of feedback were with specific components and their locations, this was mostly covered by my first question. This one adds to it my arbitrary looking placement of my resistors on the PCB. Though it looks arbitrary the placement was based on using the space efficiently for the tracks connecting items. This does still highlight an area that can be improved. Striking a balance between the two rather than focusing on just one would make me better at both in the long run.

---
<br><br> <!-- Extra line break -->

### 11. **Maze Navigation - Arduino IDE**
<br><br> <!-- Extra line break -->
This simple code helps Algernon traverse the maze, it is a mixture of basic functions reacting to thresholds set to readings from the TCRT's in CM

```cpp
// Algernon Current Code

// LED pins
int ledR = 20;
int ledW = 18;
int ledB = 19;

// motor pins
int motor_leftA = 0;   // pin0
int motor_leftB = 1;   // pin1
int motor_rightB = 2;  // pin2
int motor_rightA = 3;  // pin3

// TCRT pins
int TCRT_Left = 26;
int TCRT_Front = 27;
int TCRT_Right = 28;
int TCRT_Output;

bool Front = false;
bool Left = false;
bool Right = false;

int drive_Speed = 35;
int turn_Speed = 30;
int reverse_Speed = 25;

bool firstLoop = true;

void setup() {

  Serial.begin(9600);

  // TCRTS
  pinMode(TCRT_Left, OUTPUT);
  pinMode(TCRT_Front, OUTPUT);
  pinMode(TCRT_Right, OUTPUT);

  // motors
  pinMode(motor_leftA, OUTPUT);
  pinMode(motor_leftB, OUTPUT);
  pinMode(motor_rightA, OUTPUT);
  pinMode(motor_rightB, OUTPUT);

  // LEDS
  pinMode(ledR, OUTPUT);
  pinMode(ledW, OUTPUT);
  pinMode(ledB, OUTPUT);
}

void loop() {

  if (firstLoop) {  // have 4 second delay before starting the loop, but only for the first loop
    delay(4000);
    firstLoop = false;
  }

  checkTcrt();  // Continuously print sensor readings for debugging
  
  Front = false;  // sensors set to false by deafult so they start by not sensing anything
  Left = false;
  Right = false;

  checkDistance();
  
  if (analogRead(TCRT_Front) < 981) {
    Serial.println("Front sensor triggered");
    Front = true;

  }
  if (analogRead(TCRT_Left) < 995) {
    Serial.println("Left sensor triggered");
    Left = true;

  }
  if (analogRead(TCRT_Right) < 993) {
    Serial.println("Right sensor triggered");
    Right = true;

  }

// If all three sensors detect something move backwards  
  if (Front && Left && Right){  
    motorsBackward();
  }
  
  else if (Front && Left){
    turnRight();
  }

  else if (Front && Right){
    turnLeft();
  }

  else if (Left){
    turnRight();
  }

  else if (Right){
    turnLeft();
  }
  
  else if (Front){
    turnLeft();
  }

  else {
    motorsForward();
  }
}

// functions
void checkTcrt() {
  // 1cm = 543 - 548, 2cm = 851 - 858, 3cm = 940 - 948,
  // 4cm = 974 - 986, 5cm = 993 - 1002, 6cm = 1002 - 1023,
  // 7cm = 1007 - 1015, 8cm = 1008 - 1018
  Serial.print(" Right Reading ");
  Serial.print(analogRead(TCRT_Right));

  // 1cm = 567 - 569, 2cm = 869 - 876, 3cm = 950 - 959,
  // 4cm = 980 - 990, 5cm = 995 - 1005, 6cm = 1003 - 1013,
  // 7cm = 1010 - 1018, 8cm = 1013 - 1021 
  Serial.print("| Left Reading ");
  Serial.print(analogRead(TCRT_Left));

  // 1cm = 691 - 700, 2cm = 892 - 898, 3cm 953 - 964,
  // 4cm = 981 - 990, 5cm = 994 - 1003, 6cm 1001 - 1011,
  // 7cm = 1007 - 1015, 8cm = 1007 - 1019
  Serial.print("| Center Reading ");
  Serial.println(analogRead(TCRT_Front));
  delay(500);
}

void checkDistance() {
  if (analogRead(TCRT_Right) < 980) {
    digitalWrite(ledW, LOW);
  }
  if (analogRead(TCRT_Right) > 980) {
    digitalWrite(ledW, HIGH);
  }
  if (analogRead(TCRT_Left) < 990) {
    digitalWrite(ledB, LOW);
  }
  if (analogRead(TCRT_Left) > 990) {
    digitalWrite(ledB, HIGH);
  }
  if (analogRead(TCRT_Front) < 1005) {
    digitalWrite(ledR, LOW);
  }
  if (analogRead(TCRT_Front) > 1005) {
    digitalWrite(ledR, HIGH);
  }
}

void turnLeft() {
  analogWrite(motor_leftA, -turn_Speed);
  analogWrite(motor_leftB, turn_Speed);
  analogWrite(motor_rightA, turn_Speed);
  analogWrite(motor_rightB, -turn_Speed);
}

void turnRight() {
  analogWrite(motor_leftA, turn_Speed);
  analogWrite(motor_leftB, -turn_Speed);
  analogWrite(motor_rightA, -turn_Speed);
  analogWrite(motor_rightB, turn_Speed);
}

void motorsForward() {

  analogWrite(motor_leftA, drive_Speed);
  analogWrite(motor_leftB, -drive_Speed);
  analogWrite(motor_rightA, drive_Speed);
  analogWrite(motor_rightB, -drive_Speed);
  
}

void motorsBackward() {
  analogWrite(motor_leftA, -reverse_Speed);  // Reverse left motor
  analogWrite(motor_leftB, reverse_Speed);   // Reverse left motor
  analogWrite(motor_rightA, -reverse_Speed); // Reverse right motor
  analogWrite(motor_rightB, reverse_Speed);  // Reverse right motor
}

void allLeds() {
  digitalWrite(ledR, HIGH);
  digitalWrite(ledW, HIGH);
  digitalWrite(ledB, HIGH);
}
```

<br><br> <!-- Extra line break -->

---

### 12. **Extras - Fusion 360**

In the final testing section certain problems arose, namely tight corners the mouse would get caught between the chassis and the side TCRT's so I designed a basic bumper that would help redirect the mouse (mostly). This was done by taking basic measurements of the front of the chassis and then adding small hook shapes to clip the bumper to the mouse. Using the basic measurements make an arrow shape and then extrude up by 5mm. 

<br><br> <!-- Extra line break -->

<table>
  <tr>
    <td style="text-align: center;">
      <b>Bumper</b><br>
      
    </td>
    <td style="text-align: center;">
      <b>Printed Bumper</b><br>
      
    </td>
  </tr>
</table>

<br><br> <!-- Extra line break -->

And for the last part the MDF wheels were having difficulties gripping the ground so I designed tires that would fit over the wheels with a groove for elastic bands to rest in. Firstly make a circle the same diameter as the wheels 38mm and then offset this by 1mm and extrudes the width of the MDF which was 6mm. I then offset the larger circle again on either side and extruded inwards by 2mm. Then I decided to make it so the tire couldnt slide off the wheel by making a third offset, but this one would be a smaller circle effectively making them like caps on the wheels. Then the outer edge was filleted. 
<br><br> <!-- Extra line break -->

<table>
  <tr>
    <td style="text-align: center;">
      <b>Fusion tire</b><br>
      
    </td>
    <td style="text-align: center;">
      <b>Printed Tire</b><br>
      
    </td>
  </tr>
</table>

## License  
This project is licensed under the MIT License. See the [LICENSE](LICENSE) file for details.

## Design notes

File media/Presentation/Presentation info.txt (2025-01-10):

Viewing the file powerpoint version of this presentation changes the orientation of the imbedded videos

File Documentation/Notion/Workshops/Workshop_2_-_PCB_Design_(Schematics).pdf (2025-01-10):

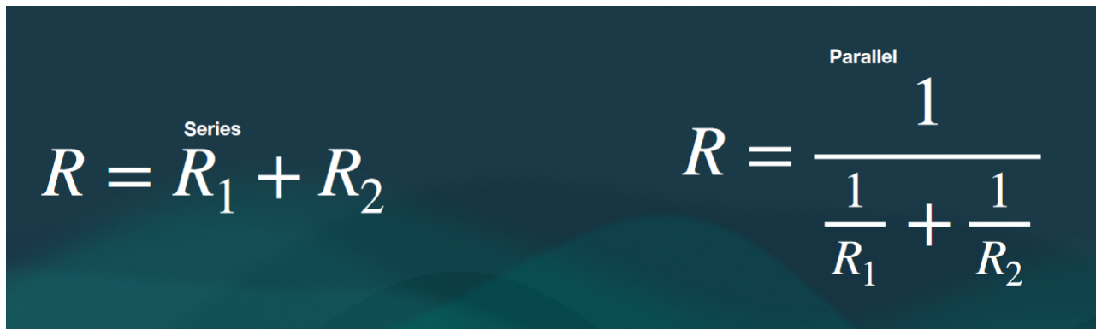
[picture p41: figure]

Workshop 2 | - PCB Design | (Schematics) | 1

# Workshop 2 - PCB Design (Schematics)

Friday 4th October
Lecture PCB’s (Printed Circuit board)

Today we looked into making PCB’s and were shown how to design one is EASYeda. Within this we can find the components we need through various searches, of which the User Contributed was very helpful.

We were also shown how to evaluate resistors in series and parralel and were given some homework (see below)

We were also pointed towards the symbol standard of IEC rather than ANSI because IEC is more of a global standard as opposed to ANSI which is just America.

Home Work

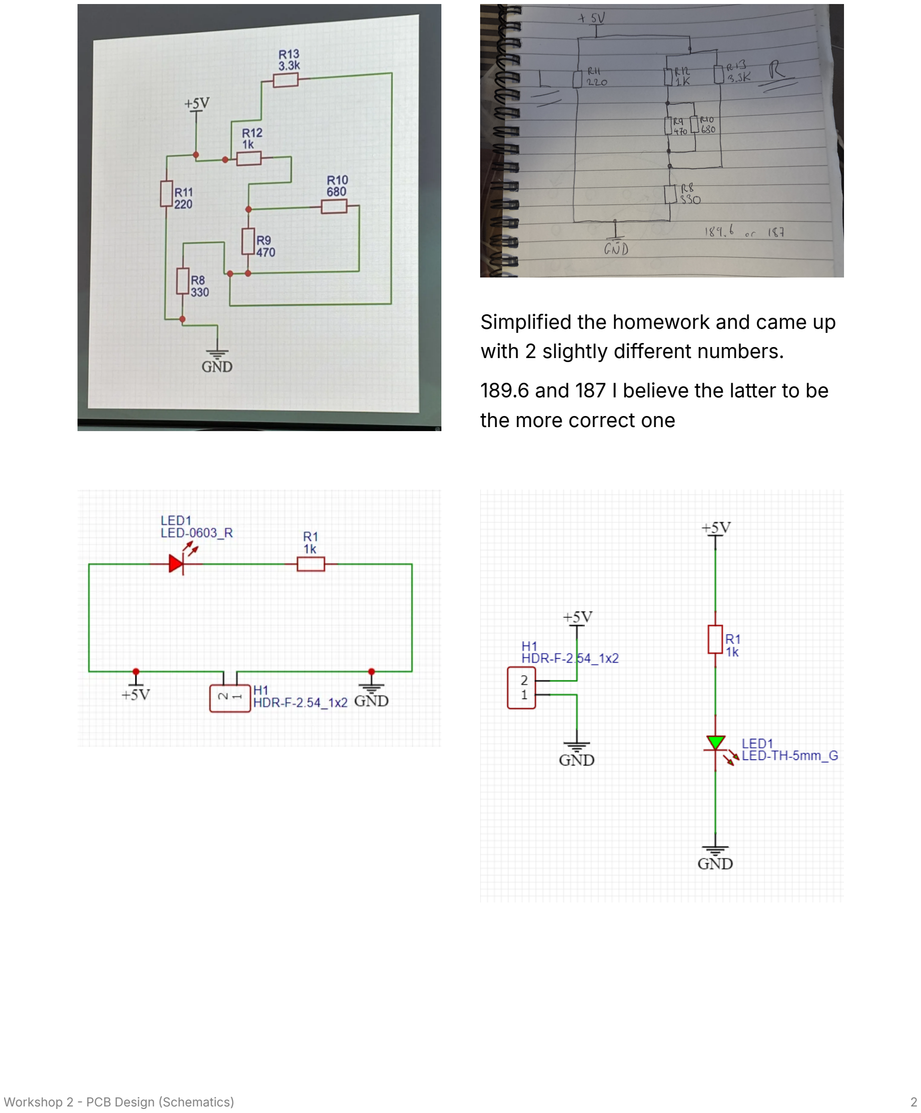
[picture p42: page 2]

Workshop 2 | - PCB Design | (Schematics) | 2

Simplified the homework and came up with 2 slightly different numbers. 189.6 and 187 I believe the latter to be the more correct one

## Setup and Layout

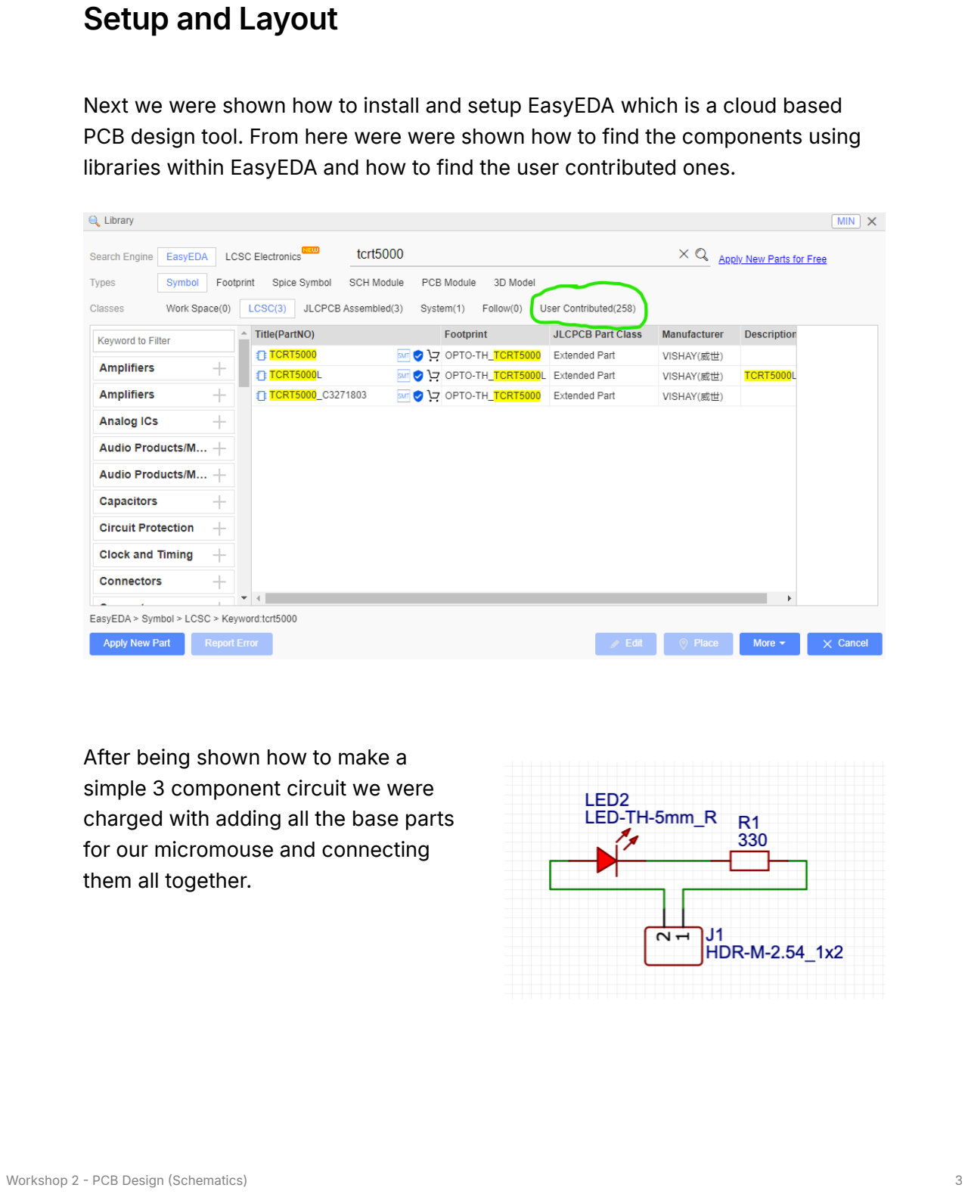
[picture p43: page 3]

Workshop 2 | - PCB Design | (Schematics) | 3

Next we were shown how to install and setup EasyEDA which is a cloud based PCB design tool. From here were were shown how to find the components using libraries within EasyEDA and how to find the user contributed ones.

After being shown how to make a simple 3 component circuit we were charged with adding all the base parts for our micromouse and connecting them all together.


Workshop 2 | - PCB Design | (Schematics) | 4

I have decided to add one more component to the list being a compass, I am looking to adding this functionality to help the mouse navigate but always knowing the directions it faces.

I ran into a small issue Of having duplicate generic names on items withing the sheet such as R1 being used multiple times. Must remember to change them along the way, other than that linking each part was relatively painless.
The compass being an extra I had to make sure the SCL and SDA were connected to the correct GPIO pins.

SCL (Serial Clock Line): This pin carries the clock signal, which synchronizes data transfer between the sensor and the microcontroller.

Workshop 2 | - PCB Design | (Schematics) | 5

SDA (Serial Data Line): This pin carries the data between the sensor and the microcontroller.

### Component and ID’s

Pi Pico - | C7203003
Motor Driver(L293D) - | C12340
Proximity Sensor(TCRT5000) - | C2984661
Switch - | C2939728
Voltage Regulator (L7805) - | C347289
Compass - | HMC5883L

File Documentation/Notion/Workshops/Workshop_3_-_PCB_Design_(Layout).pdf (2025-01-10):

# Workshop 3 - PCB Design (Layout)

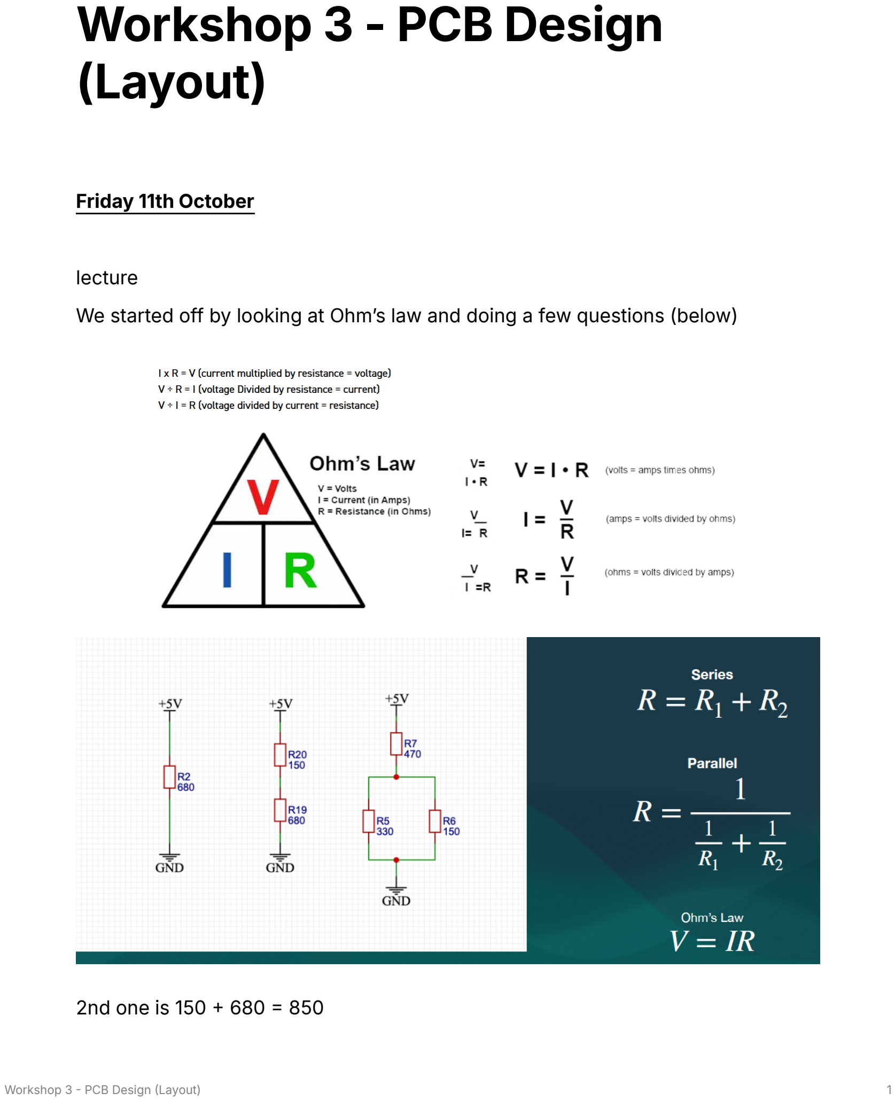
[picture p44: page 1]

Workshop 3 | - PCB Design | (Layout) | 1

Friday 11th October

lecture
We started off by looking at Ohm’s law and doing a few questions (below)

2nd one is 150 + 680 = 850

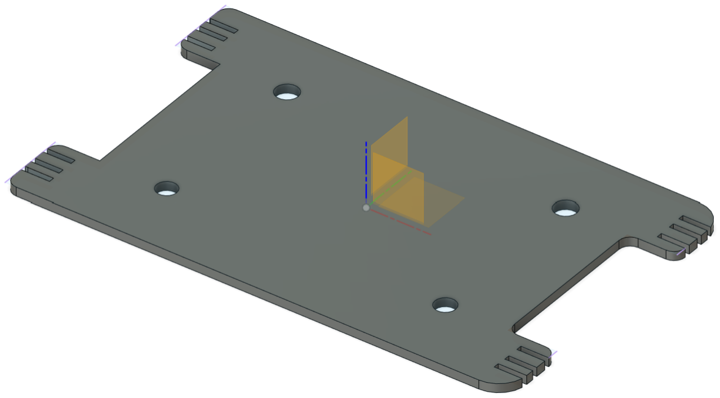
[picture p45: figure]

Workshop 3 | - PCB Design | (Layout) | 2
5 / 830 = | 0.006
voltage between the two resistors would be 0.006 x 680 = | 4.09

After this we went into EasyEda and was shown how to import a shape from Fusion 360. The process was simple enough, we build the basic design (see below) and then we create a new sketch on the surface of the design. Finish the sketch and then right click on sketch in the right hand drop down and save as a DXF file.

I gave Algernon front and back feet using the mirror function.

Within easyEDA we press the PCB button and we are given the below style schematic, then we import the DXF file and place all the components within it. We were advised to place components in places that make sense, such as the TCRT5000’s needing to be near the edges as they will need to detect light, and items that have connecting tracks to be close to one another, although is is not always possible. This makes the puzzle-like element of connecting the tracks (known as routing) much less work.

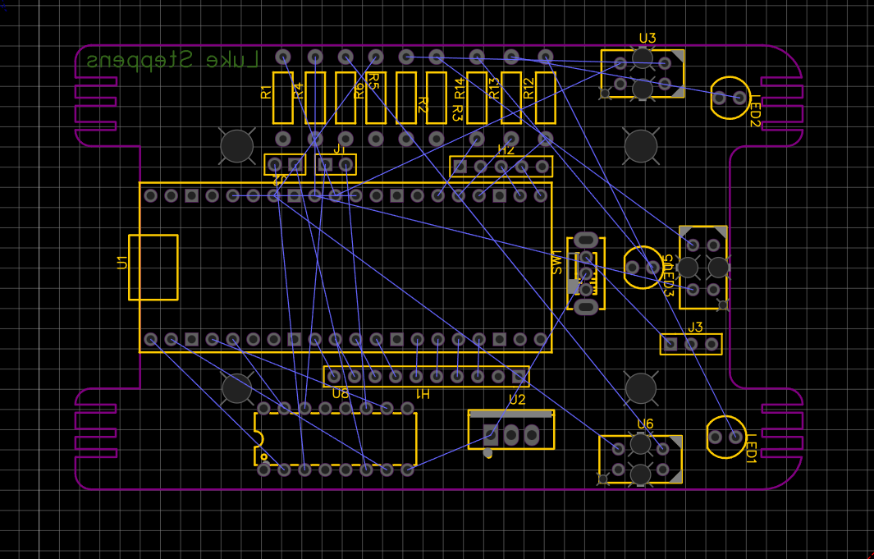
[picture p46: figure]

Workshop 3 | - PCB Design | (Layout) | 3

Note: Shorter tracks = less resistence

Another way to make the routing procedure simpler and more fun is to utilise more than one layer of the board (top and bottom in our cases) You can see red tracks on one side and blue on the other. You can always use the VIA option with creates a bridge over the same colour track buy going through to the other side of the board then back again. I havent utilised this as I wanted try and figure it all out as a test for myself.

We were shown how to add a copper layer within the PCB that way there is no need to connect ground connections, of which there are many. Alongside this we did the same with connecting all +5V removing more manual connections and saving time.

In order to make it easier for myself I decided to make the track thinner so they could navigate through the components easier. This was a mistake and when finalising the schematic and pressing the DRC button (Design Rule Check) I was greeted with over 40 errors, I attempted to fix them all one by one but was unable to claim victory and deleted them all and started again.

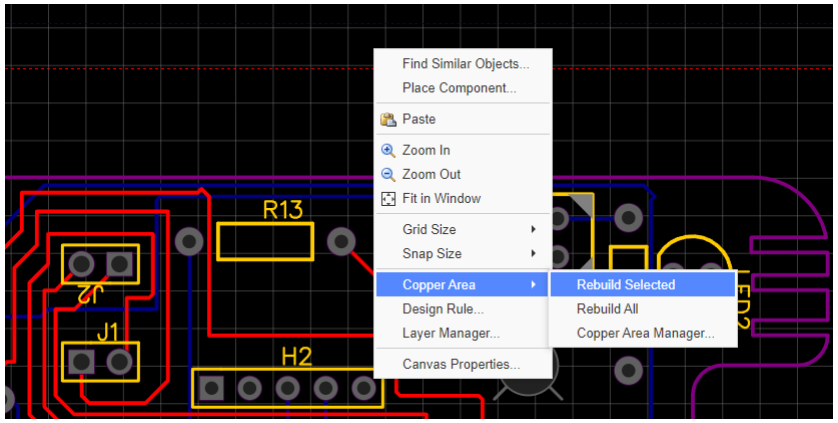
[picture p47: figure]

Workshop 3 | - PCB Design | (Layout) | 4

When editing you have to remake the copper layer mentioned above for it to fully update to any changes you have made with the tracks.

When re routing the whole board I found my style aligning with the advice given, which was to not make arbitrary lines and try to have them run alongside one another.

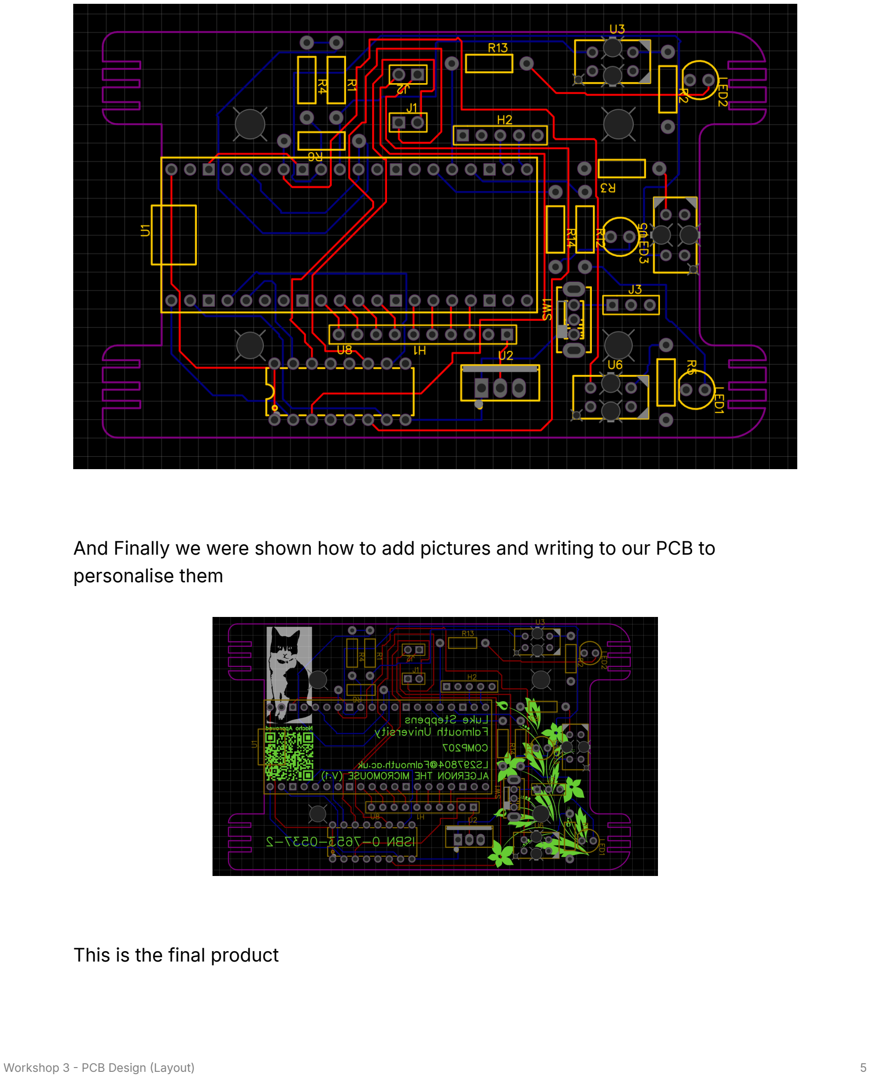
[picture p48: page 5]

Workshop 3 | - PCB Design | (Layout) | 5

And Finally we were shown how to add pictures and writing to our PCB to personalise them

This is the final product

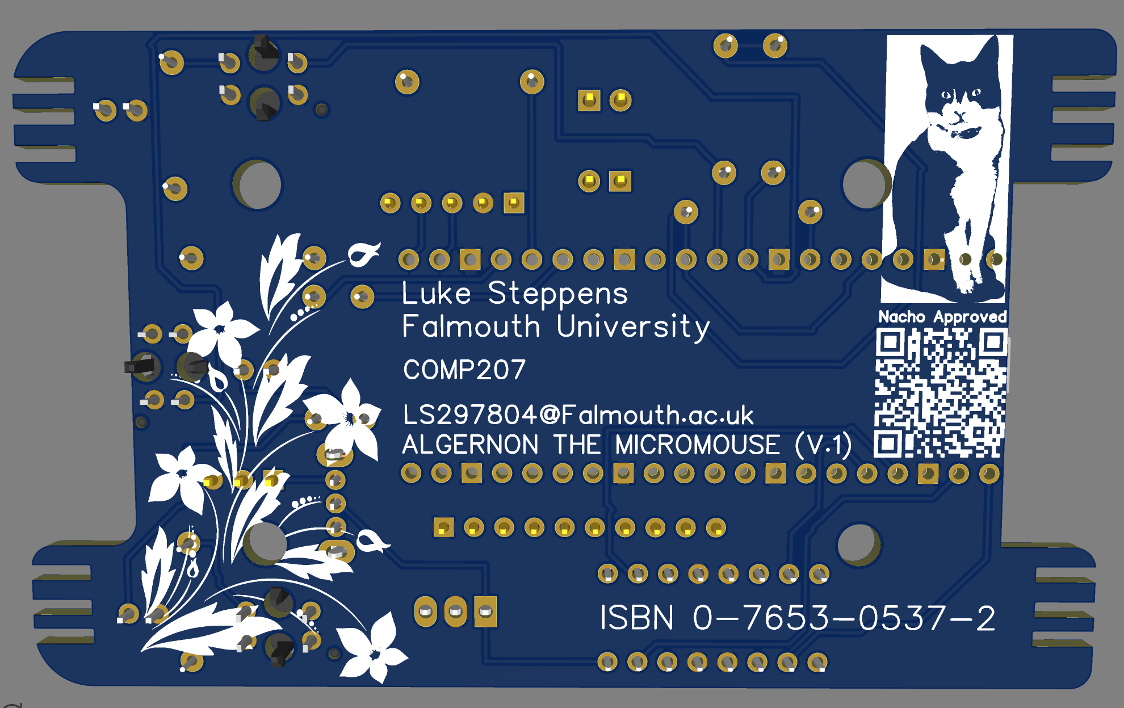
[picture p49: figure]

Workshop 3 | - PCB Design | (Layout) | 6

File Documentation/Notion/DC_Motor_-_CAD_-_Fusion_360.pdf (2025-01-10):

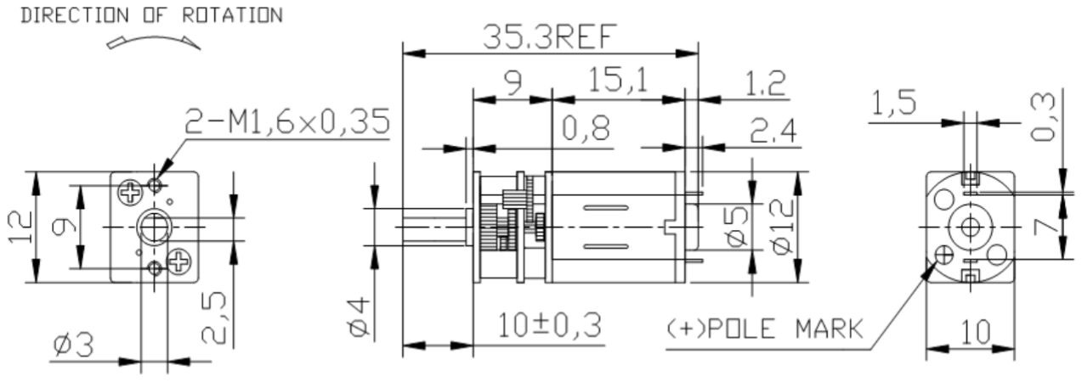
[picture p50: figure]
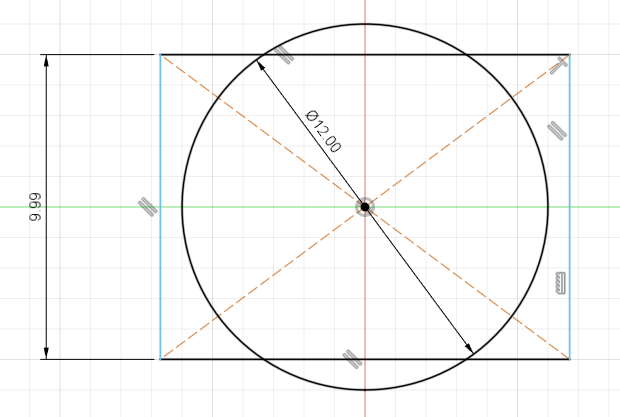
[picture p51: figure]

DC Motor | - CAD | - Fusion 360 | 1

# DC Motor - CAD - Fusion 360

For this component we were tasked with learning to create 3D from design drawings, workshop 4 contains the full lesson.

Firstly we made a new sketch and used the circle tool to create a circle with a diameter of 12mm, we overlayed a square on this circle of 9.99mm (need to ask why 9.99 again)

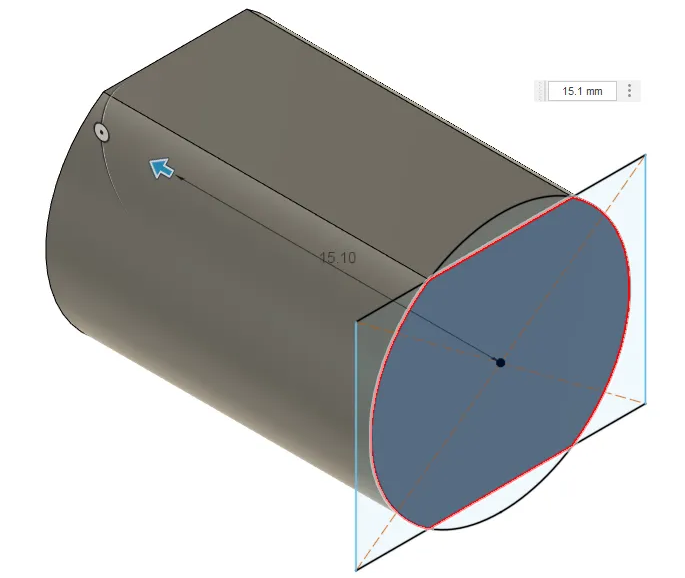
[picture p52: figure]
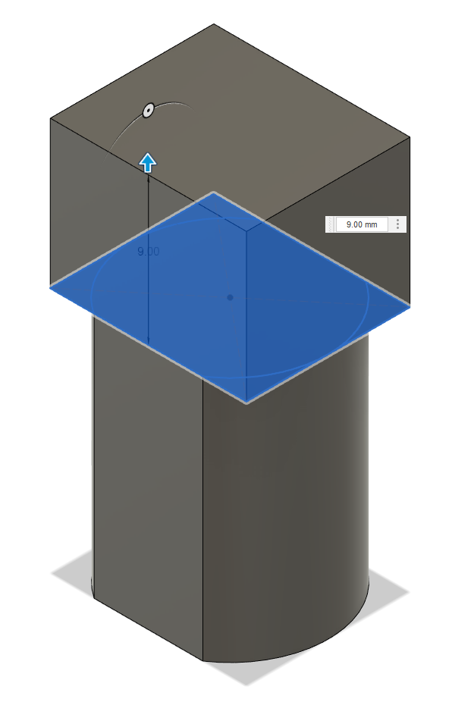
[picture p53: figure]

DC Motor | - CAD | - Fusion 360 | 2

Extruding the centre area to 15.1 gives us the main body of the motor as specified by the technical drawing.

Next I extruded from the rectangle already draw for the gearbox. Again to the specifications of the drawing.

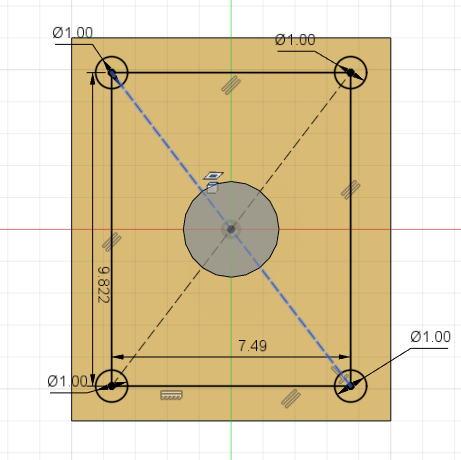
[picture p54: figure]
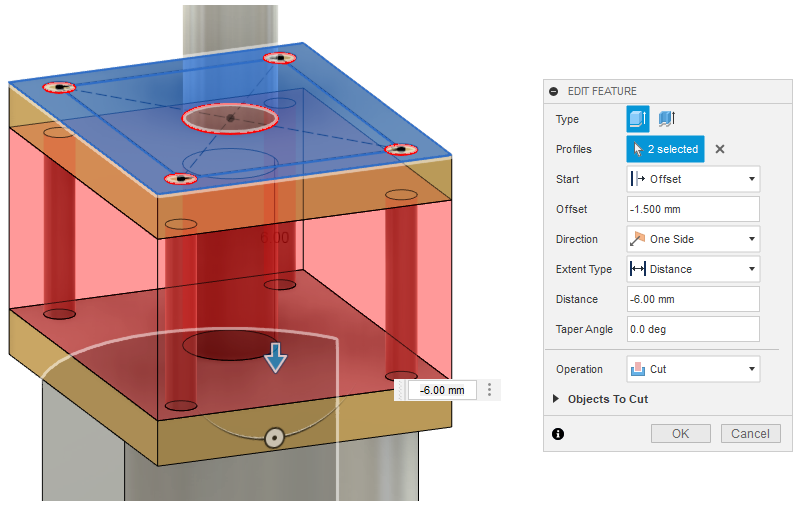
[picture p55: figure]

DC Motor | - CAD | - Fusion 360 | 3

Though the basic shape is there we were shown how to use the extrude tool in a new way which is to offset the extrude. This allowed us to create the gap section in the gearbox area. Making another sketch on the top of the gearbox I added 4 circles which would end up being the pillars.

All that was needed was the shaft and to fillet the edges and to use the appearance option to change the colours. For the shaft a new sketch was added to the top of the rectangular box and a 3mm diameter circle was added and then extruded.

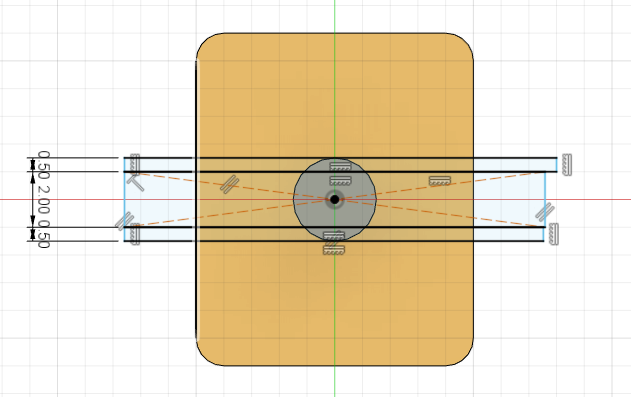
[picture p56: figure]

DC Motor | - CAD | - Fusion 360 | 4

A sketch was made on the top of the shaft, and using the centre rectangle tool I made a box with a width of 2mm. This left a 0.50mm segment on the top and bottom from which to negative extrude from one of them. This left the shape ready for a wheel to be placed upon it.

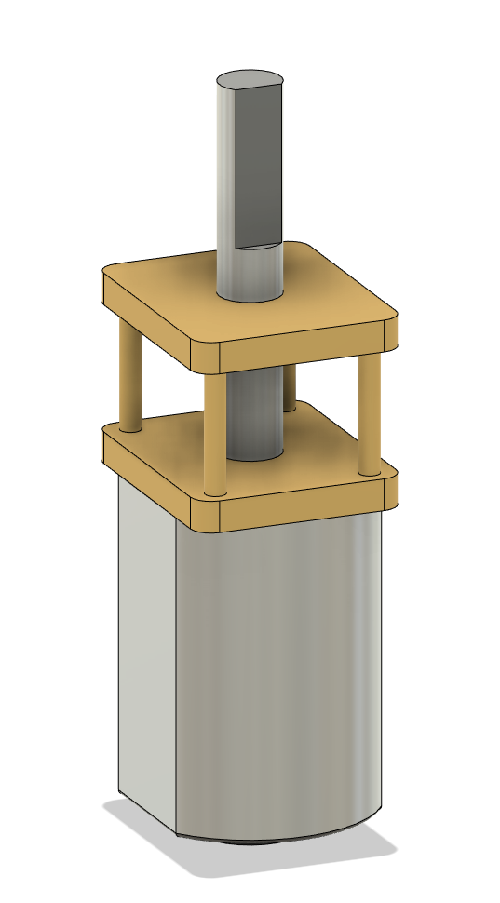
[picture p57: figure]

DC Motor | - CAD | - Fusion 360 | 5

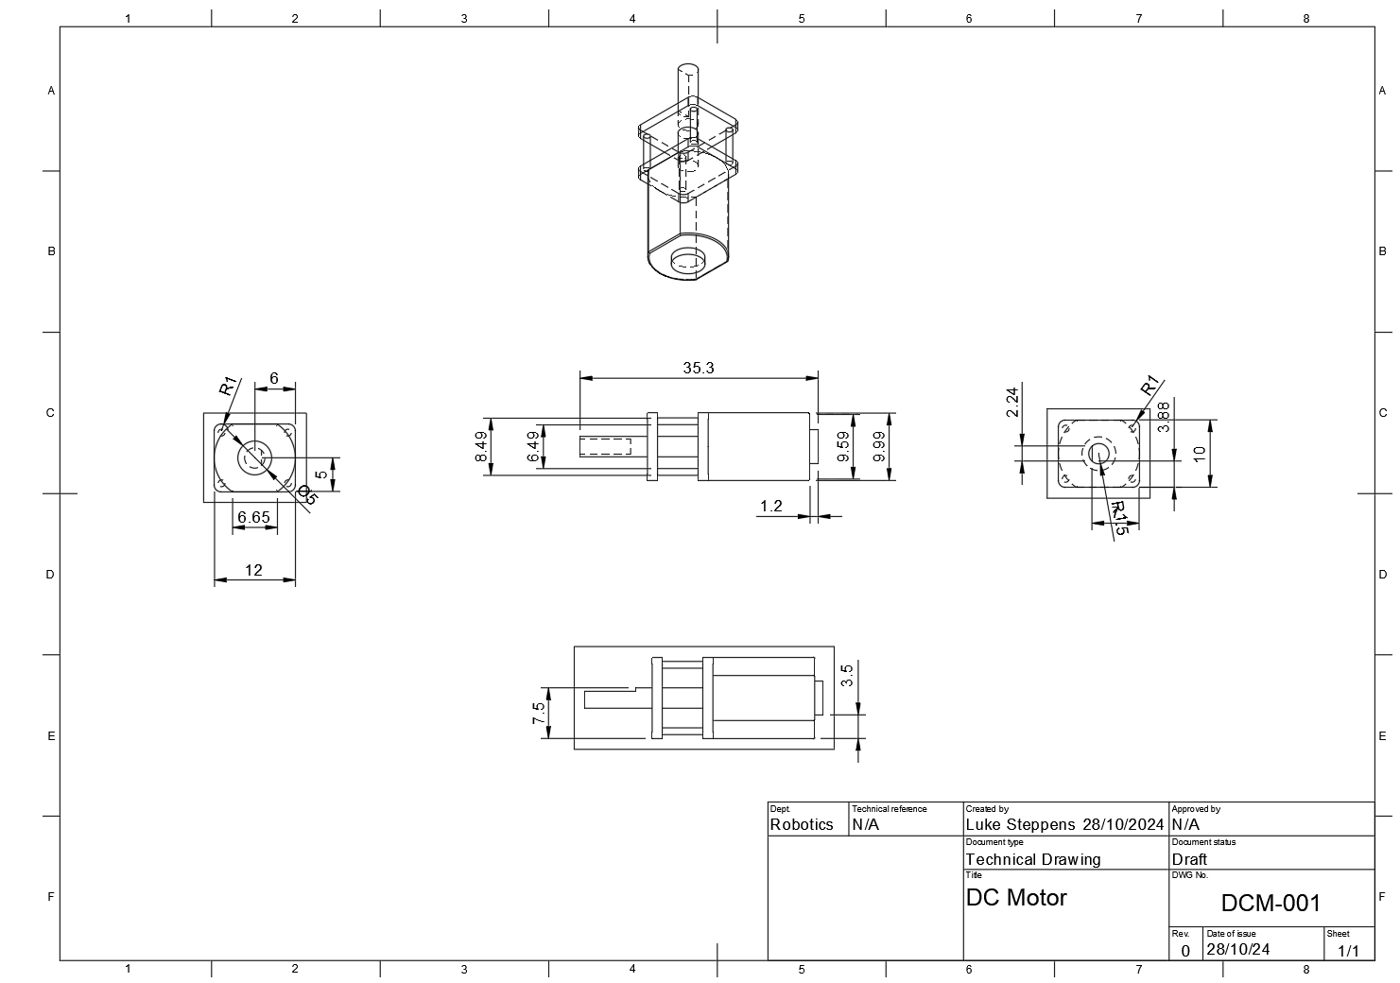
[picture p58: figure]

DC Motor | - CAD | - Fusion 360 | 6

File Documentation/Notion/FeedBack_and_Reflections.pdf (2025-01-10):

FeedBack and Reflections | 1

# FeedBack and Reflections

For this feedback form each participent was given access to this notion, along with the Github repo for the project.

Participant Name | Participant 1 | Participant 2 | Participant 3
| Charlie | Conor | Ana
If a specific area could use more attention, what would it be and why? Example options: PCB Design Fusion 360 Code Electronics setup | 9/10 The front, there’s a design difference in the LEDs used but other than that it looks grand. | 7/10 The wires don’t jut out of the board which is nice but the extra greblies and aesthetics need to be scaled to probably reduce weight and probably height. | 8/10 For future PCB redesigns the motor pins and switch could be moved to a more convenient place on the board. The fusion360 could use less attention, anything past the current 3d print state would be slight overkill.
Does the mouse cover all desired requirements to a descent degree. Example Options: Traversal Visual feedback Aesthetics Code | 9/10 It looks amazing and the code is documented very well. I’m not sure if it can solve the maze at this point. | 9/10 The micro mouse moves through the maze quite well and the coding is greatly structured and clearly commented but i think the spoil might be much and might catch on turns. | 6/10 The code could use some work as in the currently the mouse spins no matter the tcrt input.

Which component
could have a
better placement
to make the user
experience better.

8/10
The switch could
be in a more
convenient place

8/1
The position of the
battery could be
switched to the bottom
of the robot and the

7/10
The switch and the
voltage regulator can
be swapped around for
ease of access. The

Example Options:
Wheels
LEDS
Pi Pico
TCRT5000’s
Power Switch
Battery
for the user | TCRT’s on the side should be angled more towards the front for due to cone of vision. The placement of the other components is nice.

resistors also seem to
be arbitrarily placed on
the PCB.
Market Testing | COMP207 Micro Mouse - | Luke Steppens
Please score each section out of 10

Addressing feedback
Question 1. For the first question the responses go over placement of components and the over engineering of the design. These are both valid criticisms. Going forward creating simpler designs will allow for less trouble when unforeseen problems occur, having the components better placed will also work well towards keeping things simple, helping the iterative process.

Question 2. The code is the focus of the feedback for this question. While the TCRT5000's can be a little unpredictable, I have been made aware of ideas that may help that I would like to implement if there is enough time. The main thing would be having the sensors take readings on startup and use those measurements to base the movements upon. Currently they are set to fixed numbers which aren’t always true when it comes to the sensors, this can be due to natural light and shadows.

Question 3. The main point of this piece of feedback were with specific components and their locations, this was mostly covered by my first question. This one adds to it my arbitrary looking placement of my resistors on the PCB. Though it looks arbitrary the placement was based on using the space efficiently for the tracks connecting items. This does still highlight an area that can be improved. Striking a balance between the two rather than focusing on just one would make me better at both in the long run.

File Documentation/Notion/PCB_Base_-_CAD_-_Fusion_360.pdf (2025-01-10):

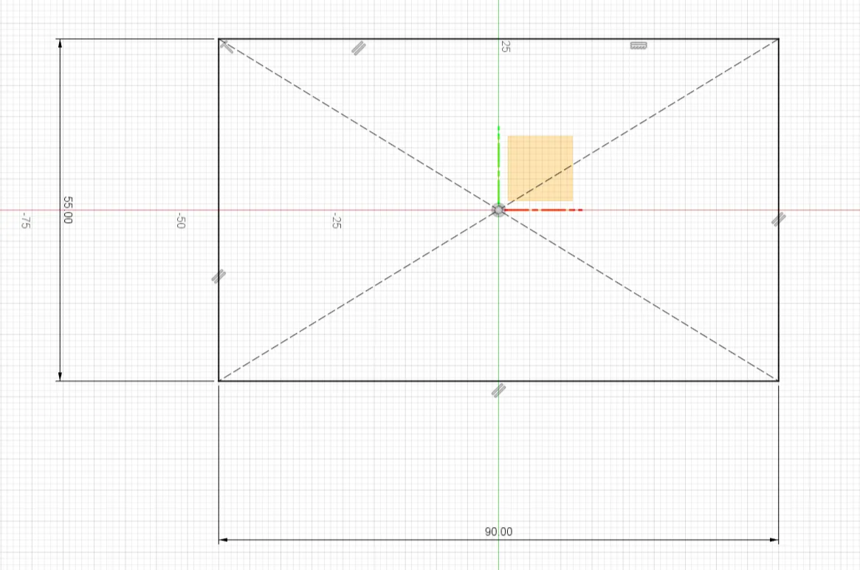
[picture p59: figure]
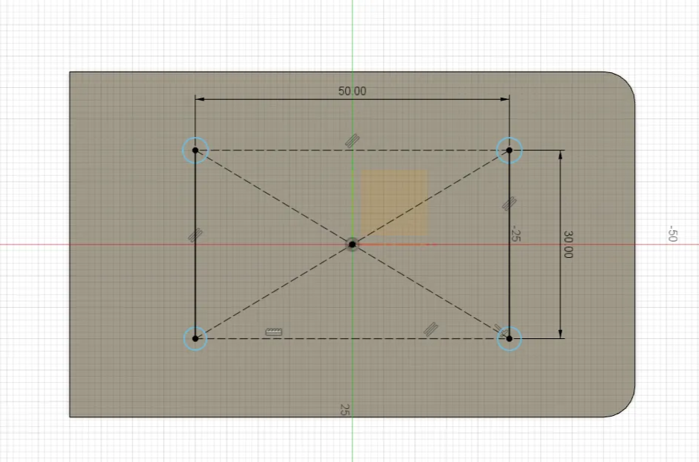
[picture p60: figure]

PCB Base | - CAD | - Fusion 360 | 1

# PCB Base - CAD - Fusion 360

CAD Modelling in Fusion 360: Initially, we were taught how to create a base for our PCB. This was to ensure all of our components would fit inside the confines and allowing for space to rearrange them and allow for wiring and maintanence. First the basic dimensions 90mm by 55mm were made with the centre rectangle tool. Followed by extruding the rectangle to 1.6mm which is the thinkness of the PCB. Next the front corners were filleted to 5mm to give it a smooth edge, and mounting holes of 3.6mm were placed 50mm away from each other horizontally and 30mm vertically apart. These were then extruded to the same thickness of 1.6mm.

With the basic design ready we were allowed to be creative, so I decided using the tools above and mirroring I would make the mouse more mouse-like. A set of small rectangles were placed on a new sketch placed on the surface of the PCB body and were then extruded making one singular paw and then I used the mirror function.

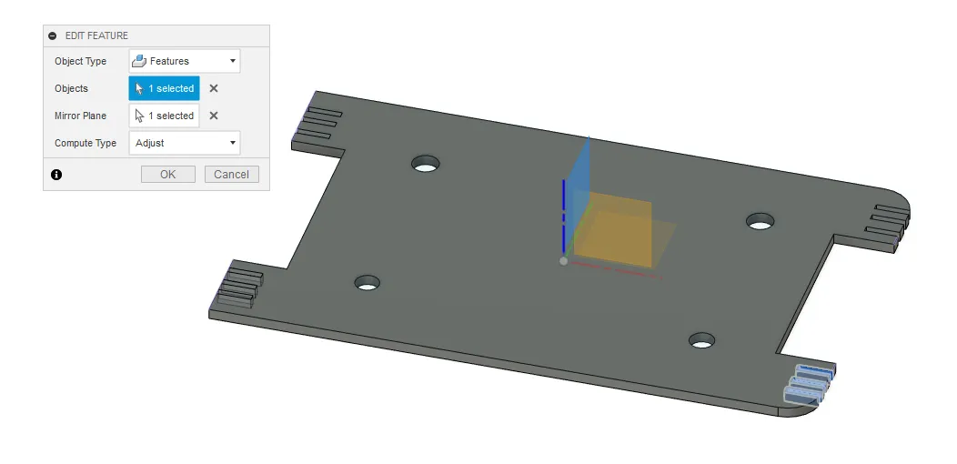
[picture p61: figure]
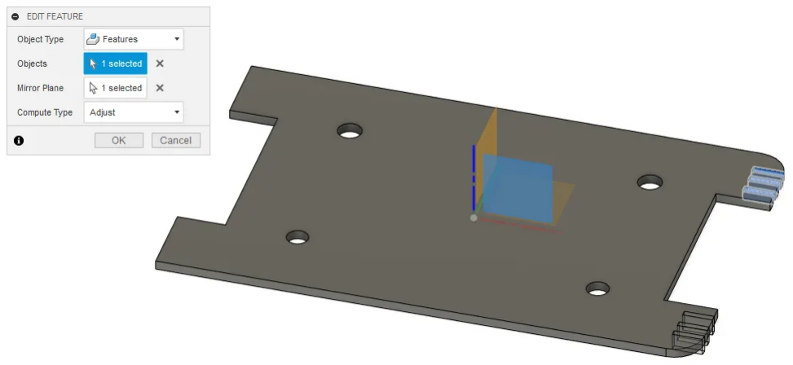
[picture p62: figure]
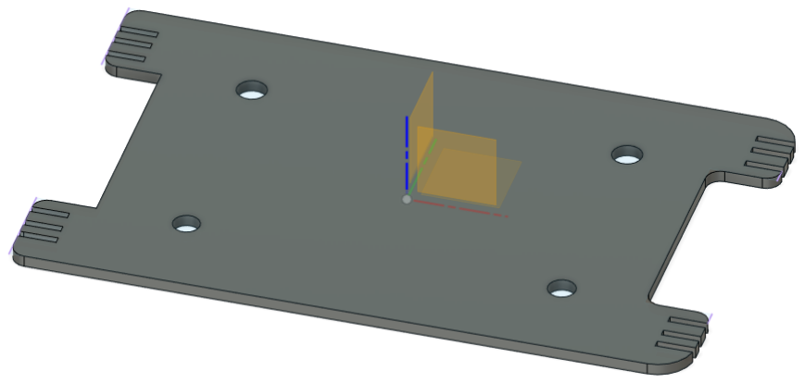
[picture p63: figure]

PCB Base | - CAD | - Fusion 360 | 2

First I mirrored across the X axis to have both the front paws identical and then across the Y axis which copied both across making all four the same dimensions. I made a shallower fillets on the back paws. Alongside a couple basic rectangular extrudes at the front and back side to make the paws stick
out.

This was made using the drawing option and using the projected views and dimensions options.

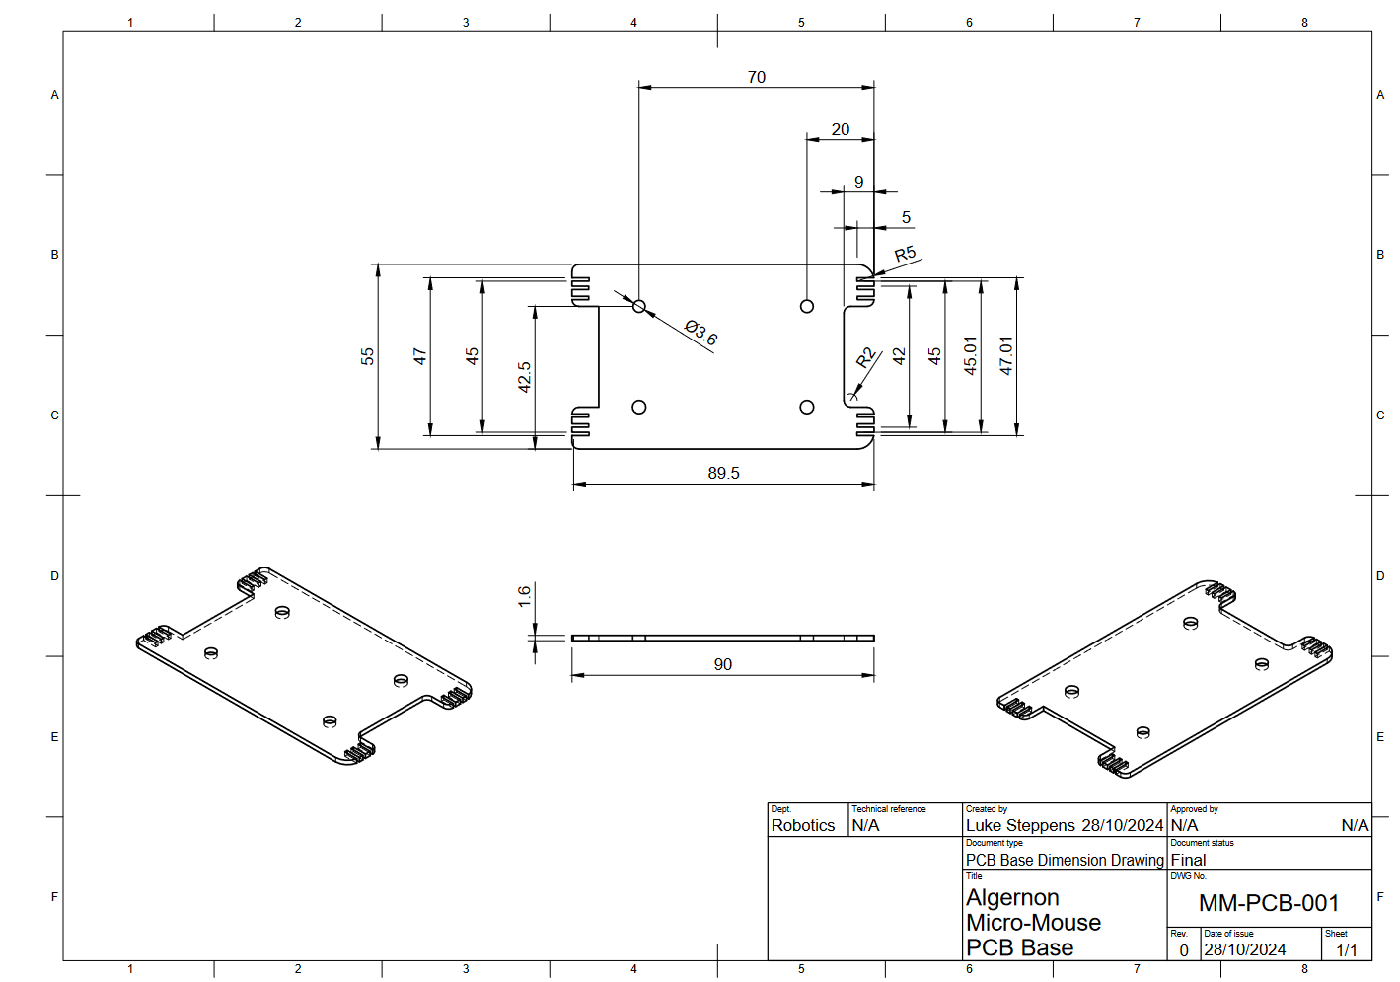
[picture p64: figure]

PCB Base | - CAD | - Fusion 360 | 3

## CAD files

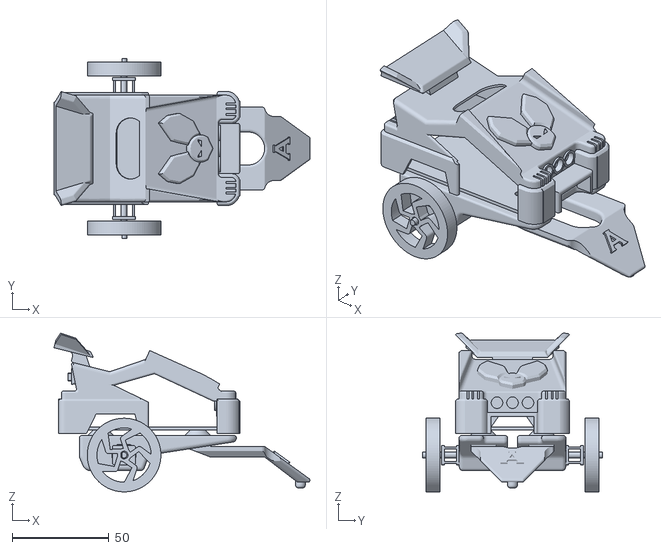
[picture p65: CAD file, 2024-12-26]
CAD/Workshop/Assembly test v15.stl
132.1 x 93.0 x 81.9

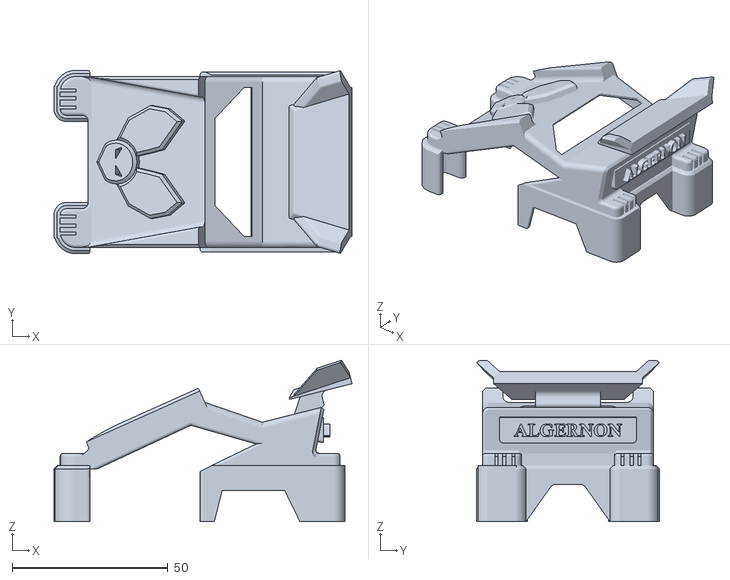
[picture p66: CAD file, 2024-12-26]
CAD/Parts/STL Files/Mouse Top Version 2.stl
95.8 x 59.0 x 51.9

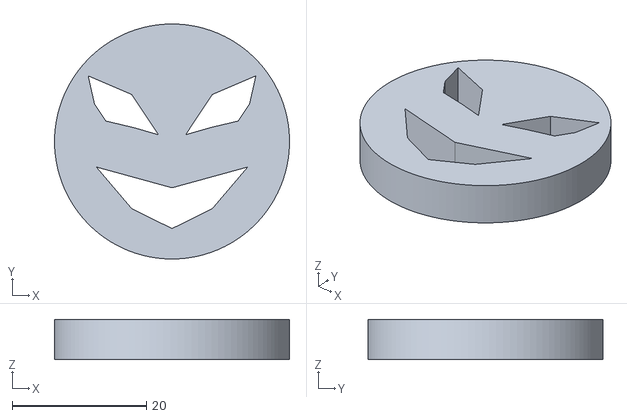
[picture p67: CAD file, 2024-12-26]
CAD/Workshop/flamedude v2.stl
35.0 x 35.0 x 6.00

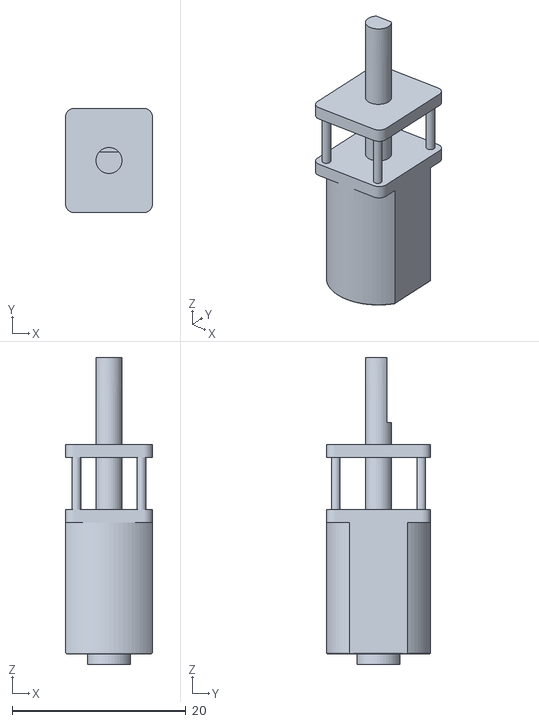
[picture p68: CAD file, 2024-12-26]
CAD/Parts/STL Files/DC Motor .stl
10.0 x 12.0 x 35.3

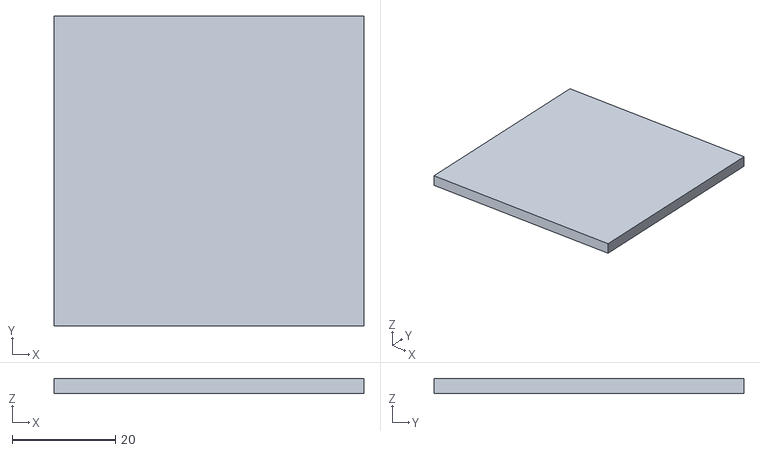
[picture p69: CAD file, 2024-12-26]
CAD/Workshop/Bottom v1.stl
60.0 x 60.0 x 3.00

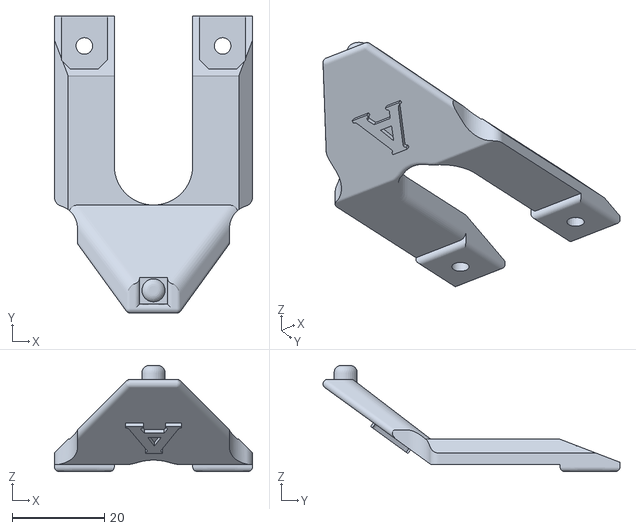
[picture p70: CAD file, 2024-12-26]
CAD/Parts/STL Files/3rd Point Balance v16.stl
43.0 x 64.4 x 23.0

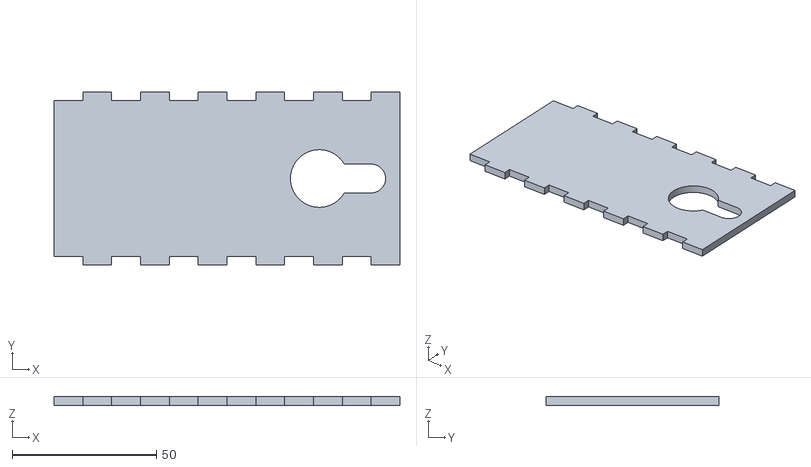
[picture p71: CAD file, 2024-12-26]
CAD/Workshop/Back v3.stl
120.0 x 60.0 x 3.00

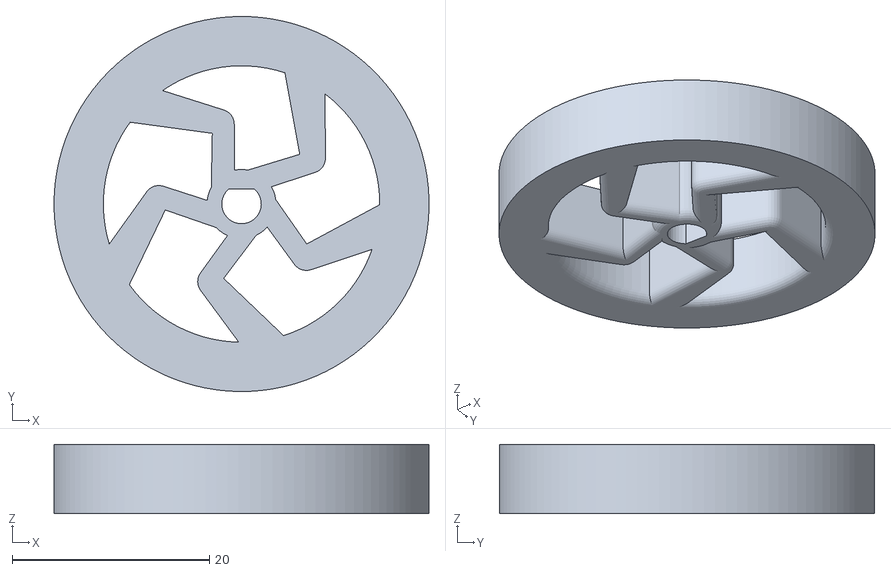
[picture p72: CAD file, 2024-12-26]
CAD/Parts/STL Files/Mouse wheel v6.stl
38.0 x 38.0 x 7.00

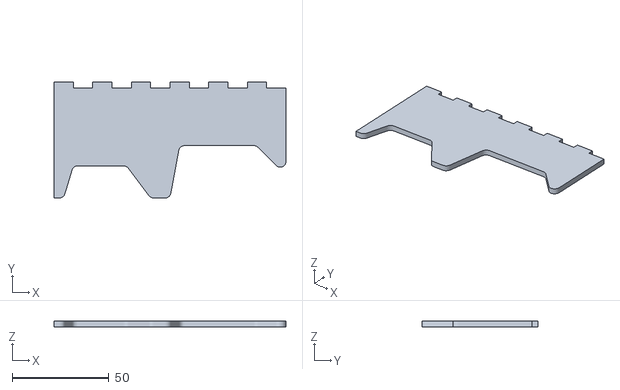
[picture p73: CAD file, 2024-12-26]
CAD/Workshop/Side v10.stl
120.0 x 60.0 x 3.00

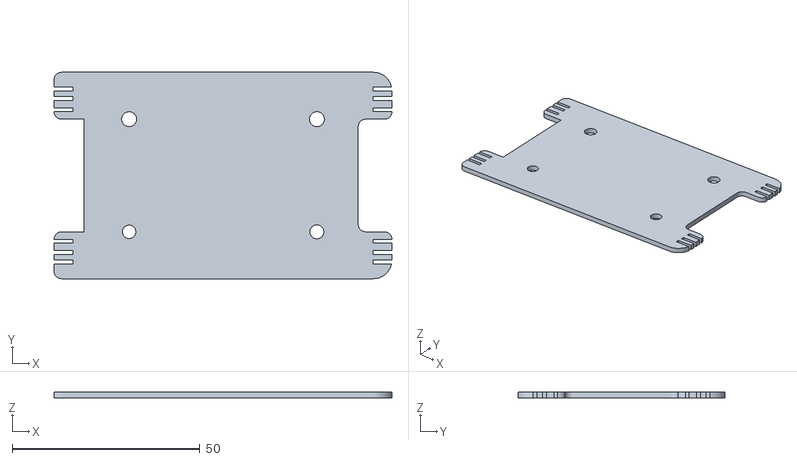
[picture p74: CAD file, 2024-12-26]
CAD/Parts/STL Files/Mouse PCB Base.stl
90.0 x 55.0 x 1.60

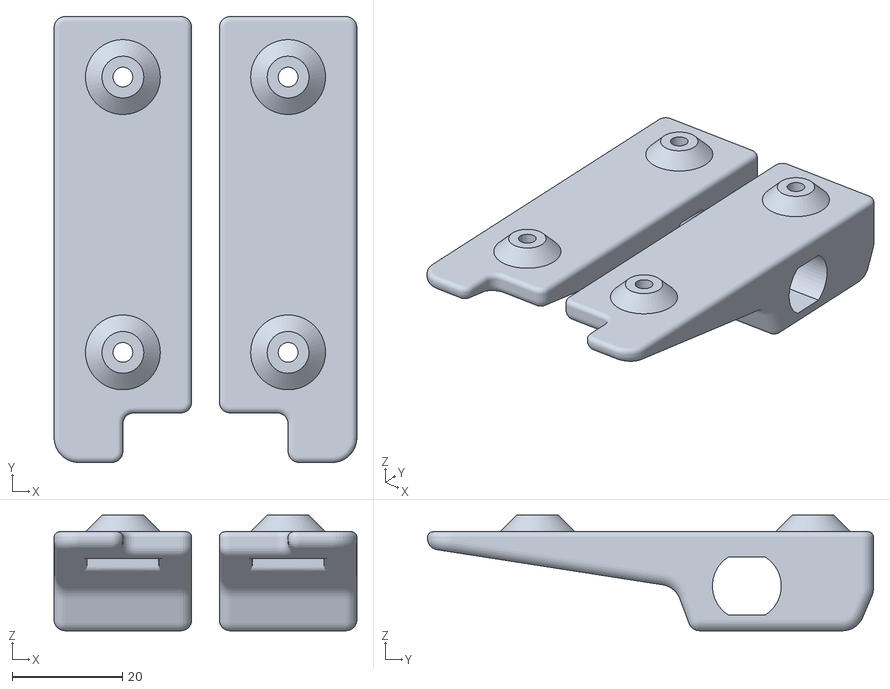
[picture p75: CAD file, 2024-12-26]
CAD/Parts/STL Files/Motor mount (Dual).stl
55.0 x 81.0 x 21.0

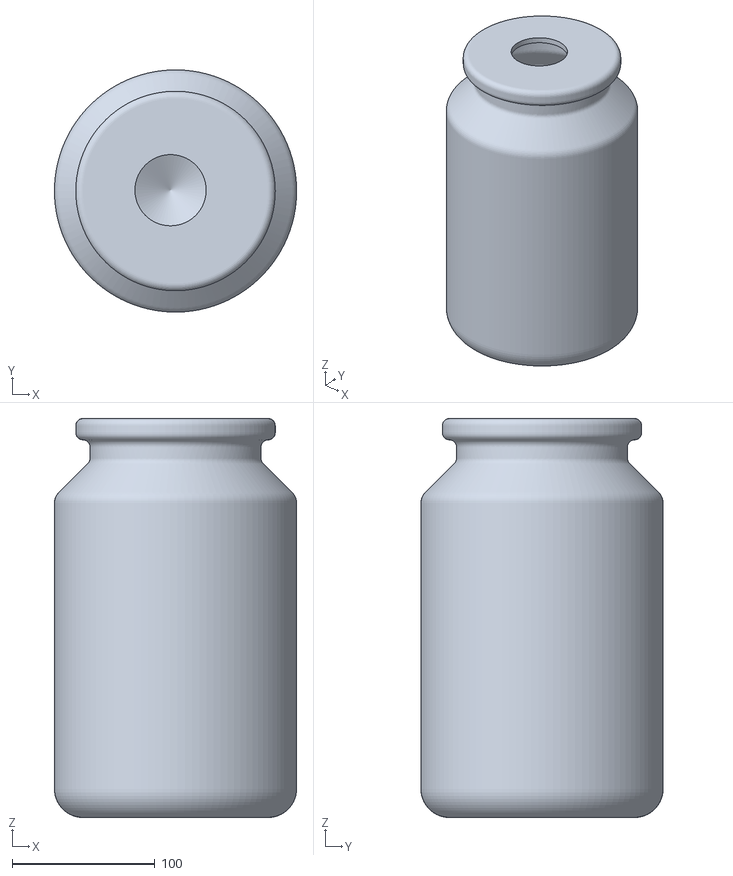
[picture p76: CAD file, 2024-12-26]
CAD/Workshop/bottle v1.stl
170.0 x 170.0 x 280.0

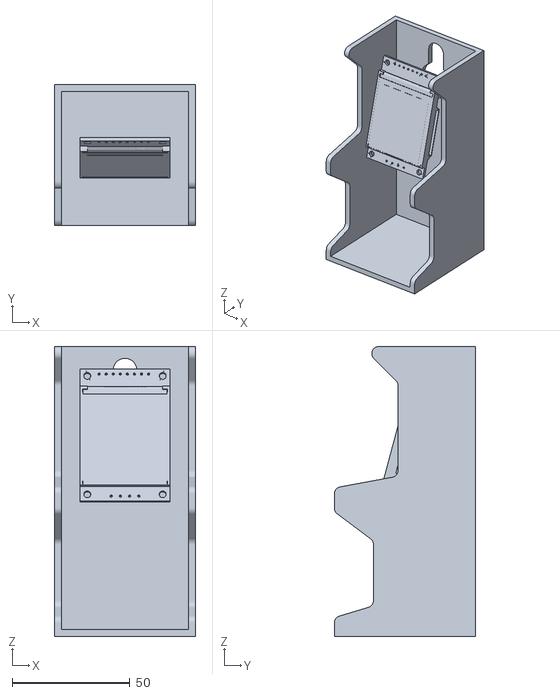
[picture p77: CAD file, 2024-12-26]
CAD/Workshop/Arcade cabinet v4.stl
60.0 x 60.0 x 123.0

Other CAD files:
CAD/Parts/Fusion Files/3rd Point Balance version 2 v2.f3d
CAD/Parts/Fusion Files/Battery holder modified v7.f3d
CAD/Parts/Fusion Files/Motor mount.f3d
CAD/Parts/Fusion Files/Mouse wheel.f3d
CAD/Parts/Fusion Files/PCB Base.f3d

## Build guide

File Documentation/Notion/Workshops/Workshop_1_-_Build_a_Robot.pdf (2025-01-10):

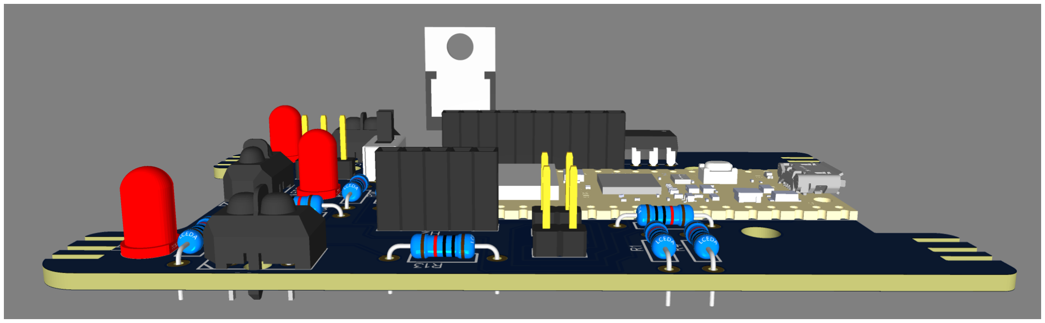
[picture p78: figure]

Workshop 1 | - Build a Robot | 1

# Workshop 1 - Build a Robot

Thursday 26th September

Today we learned how to connect a Pi Pico (micro controller) to a few components such as the TCRT5000 ir sensor (infrared) , L7805 Linear voltage regulator and a L293D H bridge via the bread board.

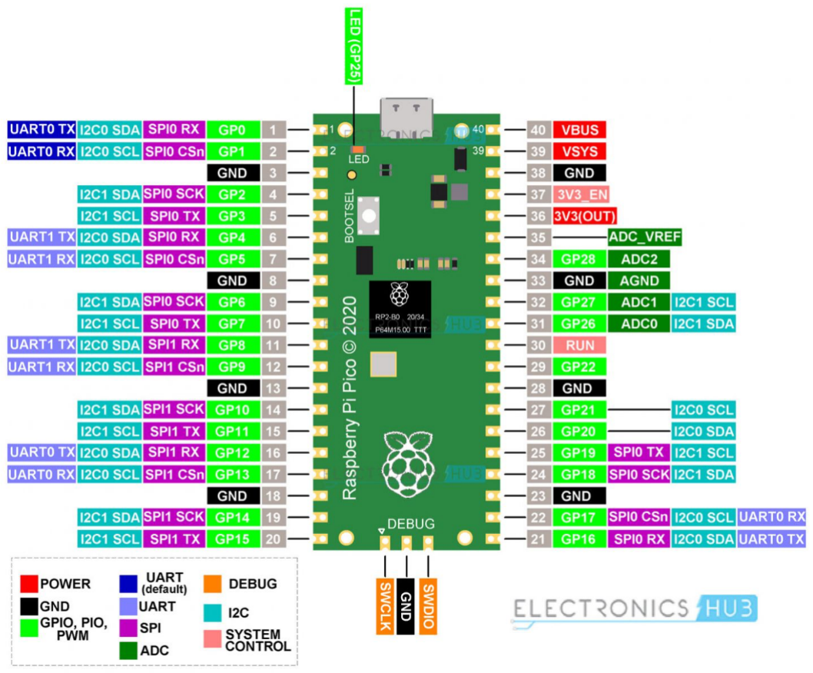
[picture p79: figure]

Utilising the arduino IDE we tested the Pi Pico after installing a core made by Earl Philhower
https://github.com/earlephilhower/arduinopico/releases/download/global/package_rp2040_index.json (https://github.com/earlephilhower/arduino-pico/releases/download/global/package_rp2040_index.json)

First we did a basic test to make the led on the Pico flash. Then we setup the linear voltage regulator to ensure the Pico always received 5 volts even if higher amounts were initially sent to it. And finally we setup the ir sensor and had it output to the serial monitor, this way we could see the numerical change and graphed those numbers in real time.

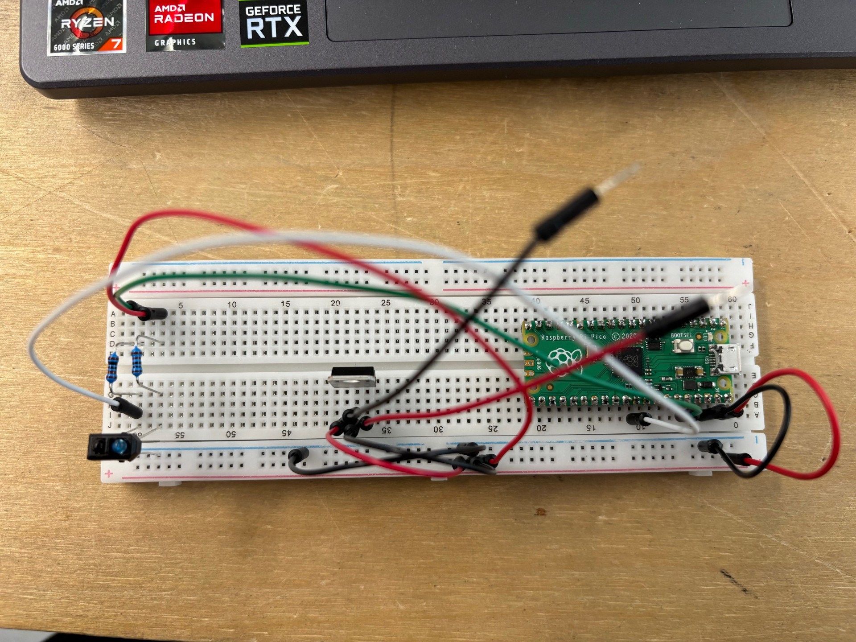
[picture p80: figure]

https://prod-files-sec
ure.s3.us-west-2.ama
zonaws.com/6d327d7
1-a800-4bb7-a305-2
462de459e8c/dc5a5
b70-5988-48d9-8b3
7-66a5bb072acc/Vid
eo.mov (https://www.notion.so/signed/https%3A%2F%2Fprod-files-secure.s3.us-west-2.amazonaws.com%2F6d327d71-a800-4bb7-a305-2462de459e8c%2Fdc5a5b70-5988-48d9-8b37-66a5b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)

# Memorable Component info

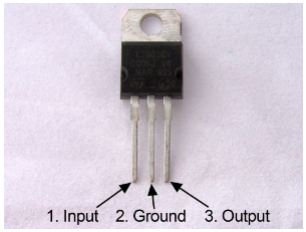
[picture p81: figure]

1. While the Arduino uno has an
onboard voltage regulator the Pi
Pico does not. This is why we use
the L7805 voltage regulator to ensure the Pico only get the required 5V and no higher.

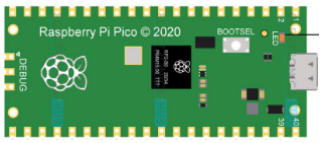
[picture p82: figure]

1. The Pi Pico has 26 multifunction GPIO pins out of 40.


1. The TCRT5000 contains both a Infra-red light emitting diode and an infra-red light dependant resistor.

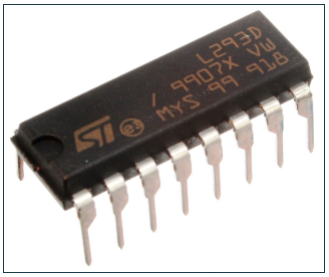
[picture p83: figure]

1. The L293D chip is a compact full H-bridge that can drive 2 motors bidirectionally. It can handle up to 1.2Amps of current and 36V

Data Sheets

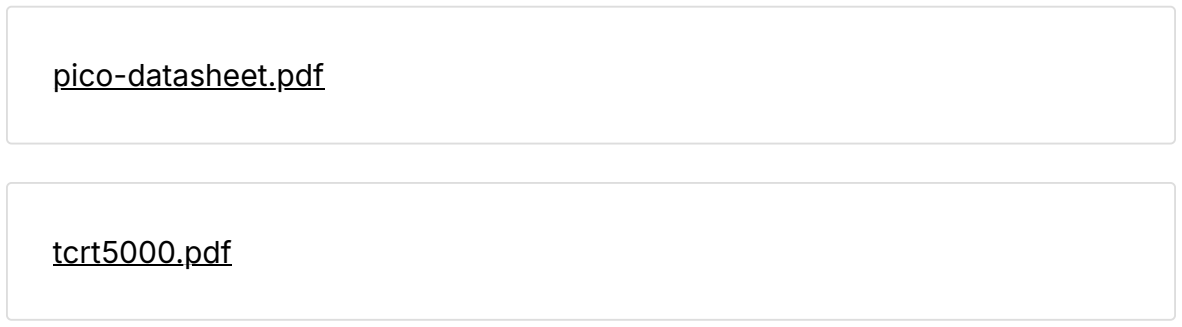
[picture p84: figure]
pico-datasheet.pdf; tcrt5000.pdf

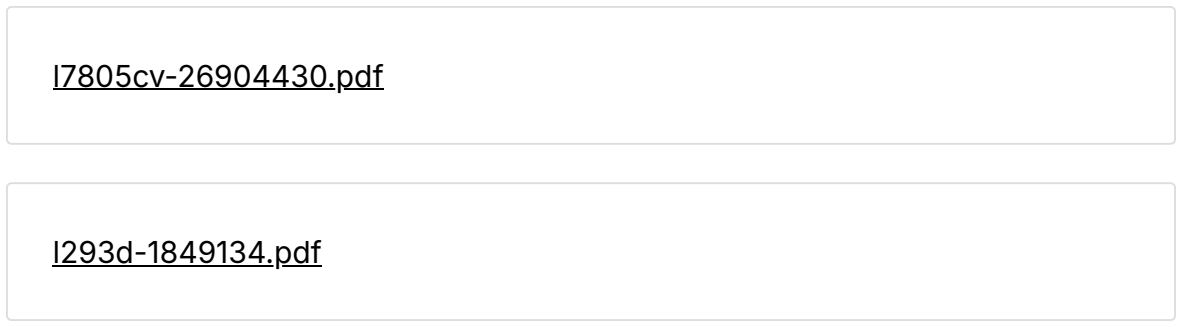
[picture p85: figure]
l7805cv-26904430.pdf; l293d-1849134.pdf

workshop info

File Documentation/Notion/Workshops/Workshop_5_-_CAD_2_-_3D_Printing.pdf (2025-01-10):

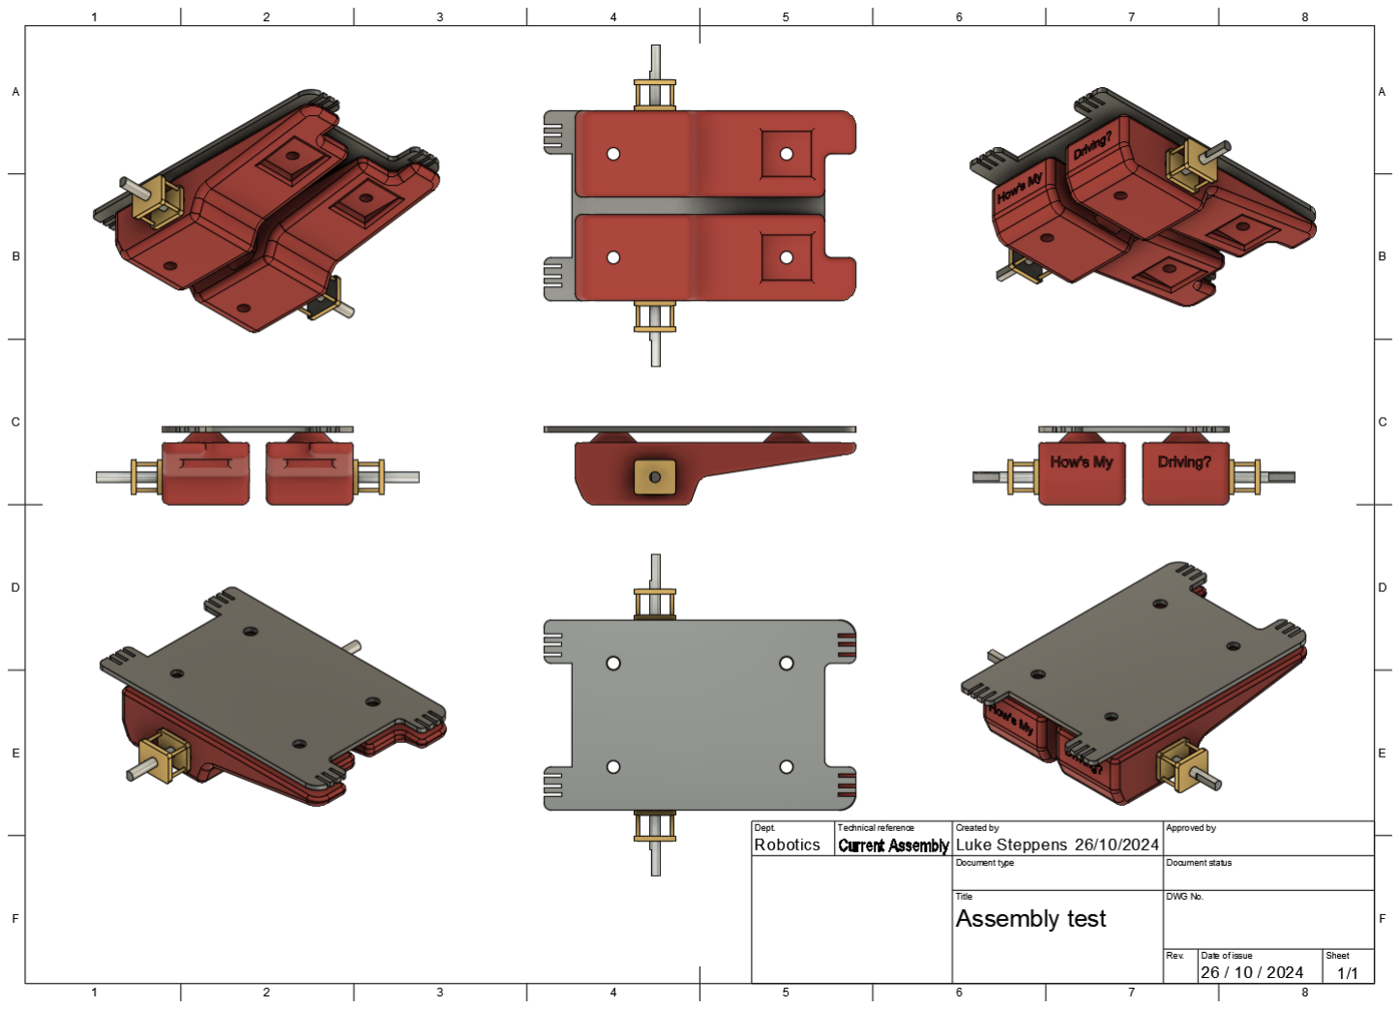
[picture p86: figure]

Workshop 5 | - CAD 2 | - 3D Printing | 1

# Workshop 5 - CAD 2 - 3D Printing

Friday 25th October

We were asked to carry on working on our motor mounts and overall assembly covering all the parts we have made.

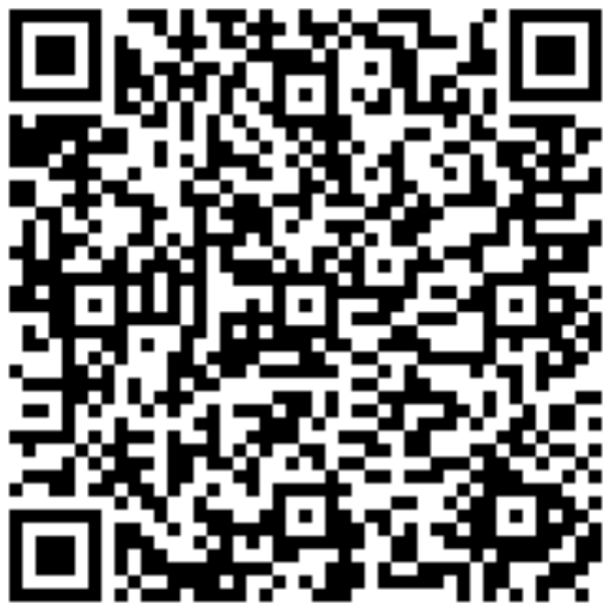
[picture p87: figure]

Workshop 5 | - CAD 2 | - 3D Printing | 2

We were then asked to start thinking of a shell and pivot point we could design for the mice.

Next we moved on to setting up our laptops to work with the laboratory 3D Printers using a program called Orcaslicer.
This is the official build not to be confused with the OrcaSlicer website which is not.
https://github.com/SoftFever/OrcaSlicer

We moved onto the device setup using this guide. 4 printers were added in total

My motor mounts had a left and write side so i chose to just print one half. First we save as mesh and we can choose the preview option where the refinement option can increase or decrease the detail by increasing or decreasing the polygons.

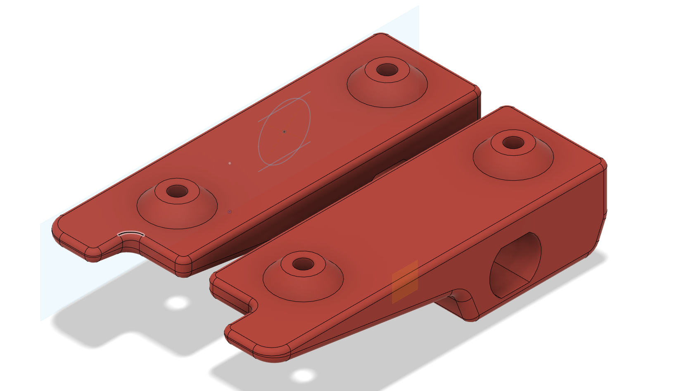
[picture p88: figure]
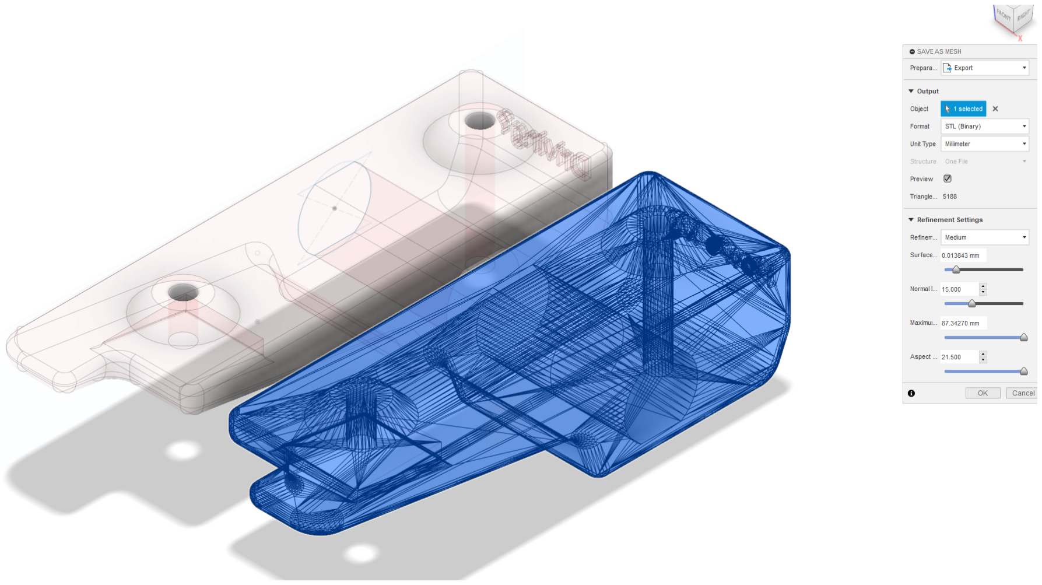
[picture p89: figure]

Workshop 5 | - CAD 2 | - 3D Printing | 3

Going back to Orcaslicer we learned of several options such as supports and strength. With supports set to tree it uses less fliament and doesnt really have a down side, then with strength our sparse infill density dictates how densly the object will be filled. The micromice being lightweight I felt no need to make it more dense. Maybe more weight will be helpful, but I that can be determined after testing.

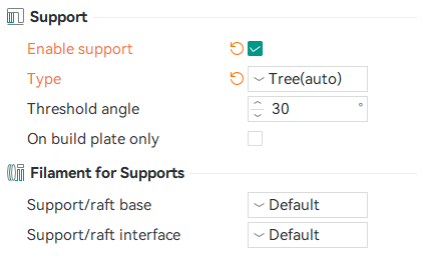
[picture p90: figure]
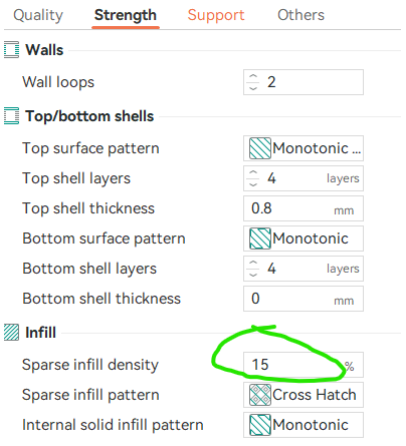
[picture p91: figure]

Workshop 5 | - CAD 2 | - 3D Printing | 4

Within the preview mode of OrcaSlicer we can look at how densly packed the infil is by using the slider on the right.

The right hand side also shows estimated time and amount of filament used.

https://prod-files-secure.s3.uswest-2.amazonaws.com/6d327 d71-a800-4bb7-a305-2462de4 59e8c/c49829ba-dc98-4af1-a9 61-952e3096e89a/IMG_3064.m ov (https://www.notion.so/signed/https%3A%2F%2Fprod-files-secure.s3.us-west-2.amazonaws.com%2F6d327d71-a800-4bb7-a305-2462de459e8c%2Fc49829ba-dc98-4af1-a961-952e3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)

With Everything ready went went across to the laboratory and printed our motor mounts.

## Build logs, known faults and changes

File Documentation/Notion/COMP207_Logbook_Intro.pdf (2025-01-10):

COMP207 Digital Prototyping Logbook | 1

# COMP207 Digital Prototyping Logbook

This logbook documents our progress in designing and fabricating a micro mouse robot using tools such as Fusion 360, EasyEDA, 3D printing, 3D scanning, laser cutting, and the Arduino IDE. The micro mouse must autonomously navigate a maze to reach the endpoint, using only onboard sensors and the provided base components.
We’ll be following the UK Micromouse Classic Rules (https://ukmars.org/contests/contest-rules/micromouse-classic/) as our competition standard.

Table of Contents (https://www.notion.so/Table-of-Contents-12d3a60eabfc80e3bf80dc9984e88903?pvs=21)

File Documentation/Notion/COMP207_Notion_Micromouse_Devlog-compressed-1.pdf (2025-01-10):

Main Project: Micromouse | 1

# Main Project: Micromouse

In this devlog, I will document the processes I followed to complete the micromouse project. This includes excerpts from various workshops that significantly contributed to different aspects of the build, as well as my independent work outside of the workshops. Both the workshops and deeper design details will be referenced and linked to their respective pages.

## Initial Thoughts

From the outset thismodule looked to allow a lot of creative thinking and problem solving to reach the literal and figurative goals. I knew I wanted to add a compass and found the magnetometer GY-271 HMC588L. This would become a stretch goal later on.

## Introduction to Components

First we were introduced to the basic components that would comprise our micromouse.
1. | Pi Pico - | Micro Controller
2. | TCRT500 - | Infra red sensor
3. | L7805 - | Linear voltage regulator
4. | L293D - | H-Bridge

We went about connecting these up with breadboards and using the Arduino’s integrated development enviroment (IDE) and installed a plugin in order to use the

Pi Pico with it. From here we tested each individual components to ensure they worked correctly and for debugging experience.

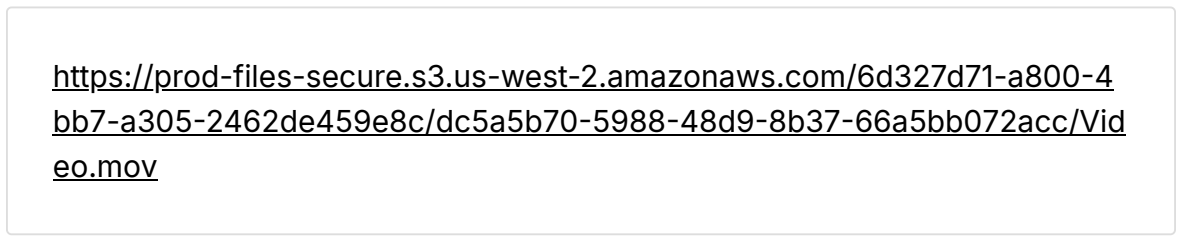
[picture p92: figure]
https://prod-files-secure.s3.us-west-2.amazonaws.com/6d327d71-a800-4 bb7-a305-2462de459e8c/dc5a5b70-5988-48d9-8b37-66a5bb072acc/Vid eo.mov

I go into more detail about each component in the corresponding workshop page Workshop 1 - Build a Robot (https://www.notion.so/Workshop-1-Build-a-Robot-12b3a60eabfc8093af76f7fb7c9c6e0f?pvs=21)

## Printed Circuit Boards - Schematics

With our components chosen and tested we moved on to creating a circuit board for them. The first stop was to use the program EasyEDA to create a schematic and add all our components to it. Once added every point needed to be connected to the correct place on the Pi Pico.

Components were often found in the user contributions section of the search.

This went well except for one mistake which was that on the compass I took information from the sellers page that was incorrect. The 5V on the compass should be 3.3V, I have learned to always go to the datasheet for each item rather than assume every seller has correct information.

I go into more detail of this process on the corresponding workshop page Workshop 2 - PCB Design (Schematics) (https://www.notion.so/Workshop-2-PCB-Design-Schematics-12b3a60eabfc80f58d68dc928ddf35d6?pvs=21)

## Printed Circuit Boards - Layout

Before we could arrange the layout of the circuit board we need a shape for it to fit within, we used the program Fusion 360 to design the general outline of our Micro

Mouse base.
The process is detailed here PCB Base - | CAD - | Fusion 360 (https://www.notion.so/PCB-Base-CAD-Fusion-360-12d3a60eabfc8040b940e831aee69869?pvs=21)

With the file exported as a DXF file it was then imported into EasyEDA. This is where the project took on a puzzle-like element as we had to arrange all the components within the confines of the mouse shape, and have them fit in a logical manner. Such as the TCRT5000’s be near the edges because they need to access light, this sounds simple enough but when twinned with having to connect up all the components tracks it becomes a bit of a juggling act to find a happy medium between the two.

Initial arrangement without considering
track between components.

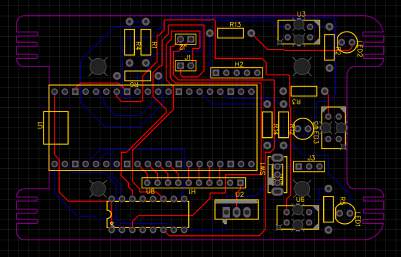
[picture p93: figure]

Final arrangement after considering component placement and track lines.

I created a problem of my own making when I i thought it would be clever to make the track lines thinner to make it easier to navigate around the board, this threw up fault after fault and I had to go back to the beginning and start again before landing on the final track design above. All that was left was to add some designs and info onto the underside of the PCB
I go into further detail on these processes in the corresponding workshop Workshop 3 - PCB Design (Layout) (https://www.notion.so/Workshop-3-PCB-Design-Layout-12b3a60eabfc80568f77fb0fecc3e167?pvs=21)

## Motor Mount - Fusion 360

Designing the mounts had to follow some basic rules in order to make sure they would fit both the DC motors and PCB’s. Firstly a sketch is placed and we begin building a basic block with holes with which to attach the PCB. The centre rectangle was made 90mm by 25mm giving lots of space, and then I used the construction line tool to find the spots 25mm away from the centre east and west. These would be the places for the PCB holes, the circle tool was used at 3.60 diameter and then used the offset tool to add another circle 2mm larger around it. The rectangle was extruded 20mm with the two circles deselected which leaves the holes going through the block.

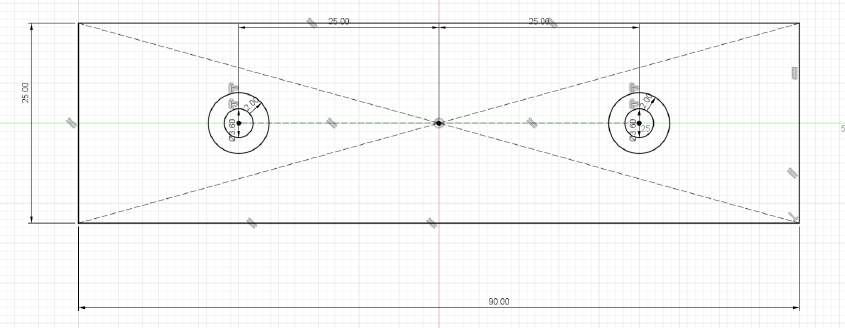
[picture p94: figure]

We were told that between the PCB and the mount we should leave 3mm for clearance, so the circles created by the offset on the surface were extruded to 3mm. Then I used the chamfer tool at 3mm on those extrusions to give a ramping down effect.

From here I used the fillet tool and rounded off most of the edges to 4mm.

The next step was to carve out the hole for the DC motor and to create the shape of the mount itself. Making the general shape was easy enough, make a sketch on the side and then used the line tool just selecting points then extruding through. The motor hole had to follow the specification of its real life counterpart so on the same sketch a circle of 12mm was made with a square of 10mm was drawn from the circles centre, this left the centre part ready for the extrusion process.

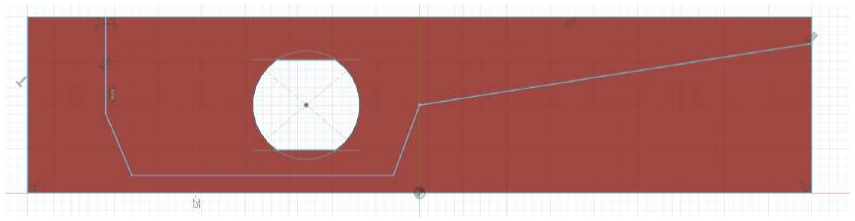
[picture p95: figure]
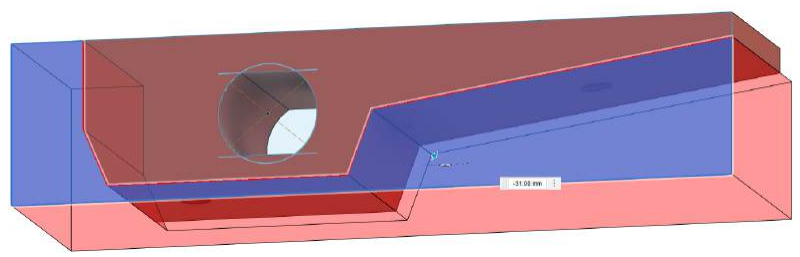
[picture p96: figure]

At this point I noticed the cylindrical hole going through on the right would where the object is at an angle, so if a screw or bolt had to sit against it, it wouldnt be able to tighten correctly.

To remedy this a sketch was made on the side of the mount what would intersect horizontally and then the two sides edit feature was used with the extrude. This way I was able to keep the gap made within the width of the motor and keep space either side. A fillet was added to the new edges of 1mm.

From here I wanted to add some character so I used the inspect tool and found out the dimensions that would have to be cut out in order to have the motor mount match the shap of the mouse poor on the PCB. 12.5mm
by 9mm. This was then extruded
through.

A 1mm fillet was added to the new angles resulting in the final shape.

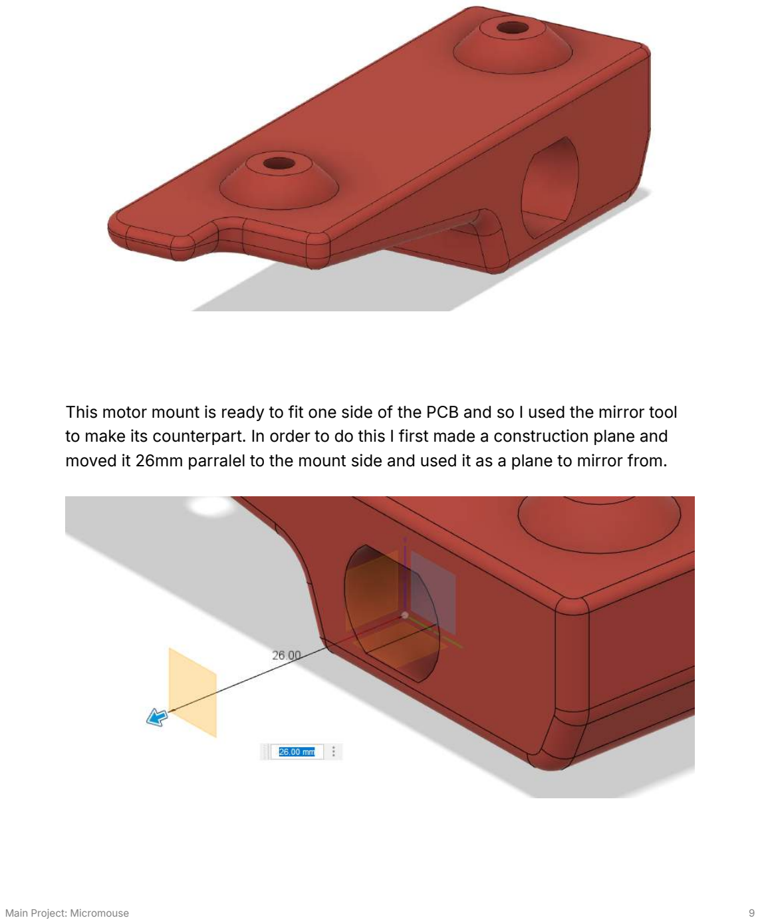
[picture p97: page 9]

This motor mount is ready to fit one side of the PCB and so I used the mirror tool to make its counterpart. In order to do this I first made a construction plane and moved it 26mm parralel to the mount side and used it as a plane to mirror from.

The last touch I put on it was to add some text to the flat surfaces on the back of each mount. This was done by putting sketches on the areas and choosing the text option. The text was moved to the centre and then extruded into the mount by 1mm

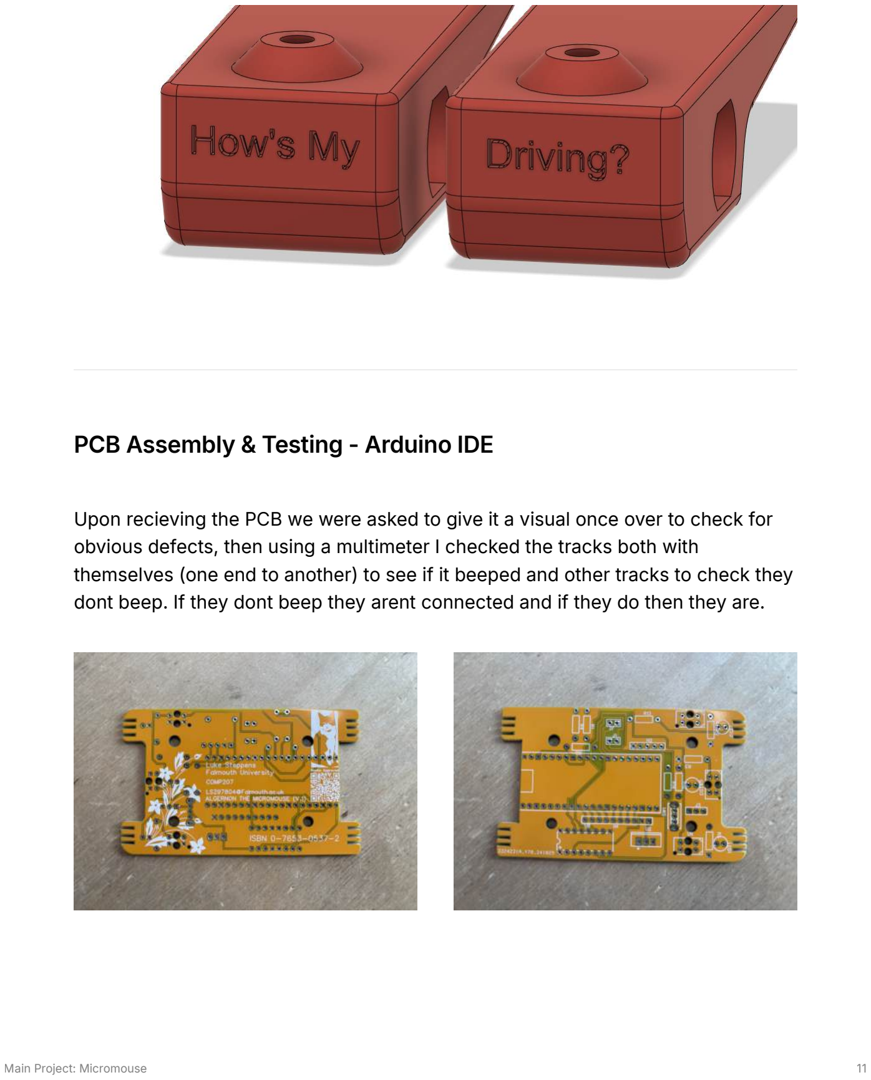
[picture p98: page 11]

### PCB Assembly & Testing - Arduino IDE

Upon recieving the PCB we were asked to give it a visual once over to check for obvious defects, then using a multimeter I checked the tracks both with themselves (one end to another) to see if it beeped and other tracks to check they dont beep. If they dont beep they arent connected and if they do then they are.

The next thing was to start attaching parts, this is where i made my first mistake and accidentally attached the Pi Pico to the wrong side effectively reversing the placement of all future components. So i started again as we recieved four PCB’s each.

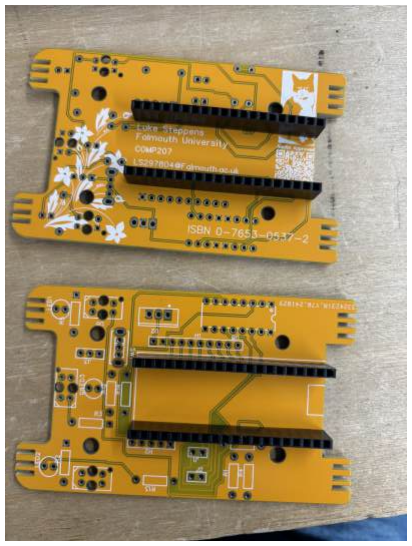
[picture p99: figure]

The bottom PCB was the correct
orientation.

From here I continued the solder components. The placement I had chosen meant that I had to add parts that were a little too close to the Pi Pico first otherwise there wouldnt be enough space later.

with basic parts added we connected to a power supply and tested the built in LED

void setup() {
pinMode(LED_BUILTIN, OUTPUT); }

void loop() {
digitalWrite(LED_BUILTIN, HIGH) delay(200);
digitalWrite(LED_BUILTIN, LOW); delay(200);
}

https://prod-files-secure.s 3.us-west-2.amazonaws.c
om/6d327d71-a800-4bb7-
a305-2462de459e8c/a9a1
be55-ab34-4b52-babc-e1
8f56ccf936/IMG_3200.mo
v (https://www.notion.so/signed/https%3A%2F%2Fprod-files-secure.s3.us-west-2.amazonaws.com%2F6d327d71-a800-4bb7-a305-2462de459e8c%2Fa9a1be55-ab34-4b52-babc-e18f5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)

The next thing was to add the TCRT5000’s and their fuses, the TCRT5000’s were fiddly and one of the LEDs came out of one so it was replaced.

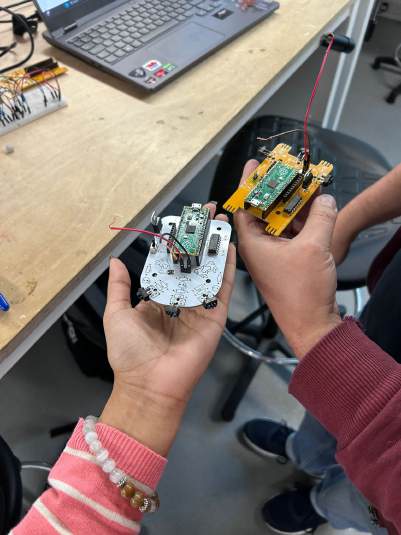
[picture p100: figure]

For the fuses I had to make sure to check the scematics as both 1k and 330 ohms resistors were needed and had to be placed correctly.

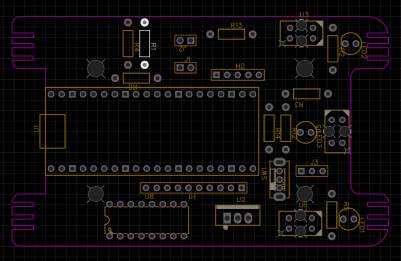
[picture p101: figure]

Using the sheet on the right I was able to twin each resistor with its placement on the PCB.

After this I soldered all of the components left over onto the PCB including some headers for the optional compass.

### Designing Chassis - Fusion 360

By far the most time was put into this section, Multiple iterations were made. The first chassis didnt have enough clearance for the voltage regulator so I lifted it. This solved one problem but highlighted another, the chassis sides were too thin and prone the snapping, so I thickened the walls only to find another problem which was that the mouse didnt fit upon the PCB base securely. So after many redesigns and additions such as LED holes and space for wires to come through the back the final design was ready.

Basic Steps

Initially I took the base PCB shape imported it into a new sketch design and extruded to 5mm, and then created a sketch on the side and used the line tool draw the general chassis shape and extruded across the base. To save time I hollowed it using the shell command and chose a thickness of minimum of 2mm.

Because the TCRT5000's have to be postitioned center, left and right we need to make sure there is a place for them so we extrude to cut a gap for them. Again this was done by creating a side sketch and extruding after drawing with the line tool.

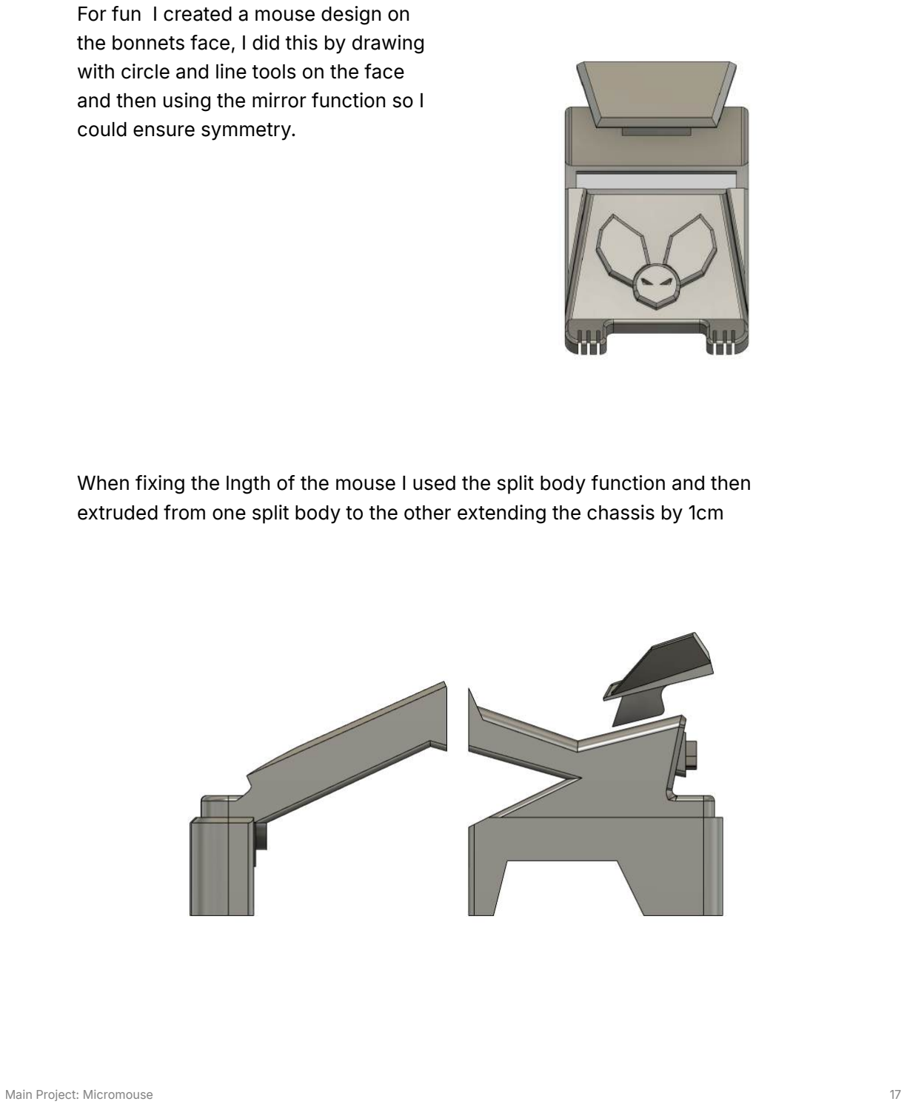
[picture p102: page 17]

For fun I created a mouse design on the bonnets face, I did this by drawing with circle and line tools on the face and then using the mirror function so I could ensure symmetry.

When fixing the lngth of the mouse I used the split body function and then extruded from one split body to the other extending the chassis by 1cm

The many iterations of the first chassis

### Assembly and Testing 2 - Arduino IDE

With the code below all three LED slots were tested and worked as hoped. I was made aware that the Blue LED was a matte type and so gave off a different more diffuse light compared to the Red and Green. The green seemed dimmer so the code was changed to lower the Blue’s intensity.

https://prod-files-secure.s3.us-west-2.amazonaws.com/6d327 d71-a800-4bb7-a305-2462de4 59e8c/6ca0a650-490a-47b0-9 da9-d4c40ea07aa9/IMG_3267. mov (https://www.notion.so/signed/https%3A%2F%2Fprod-files-secure.s3.us-west-2.amazonaws.com%2F6d327d71-a800-4bb7-a305-2462de459e8c%2F6ca0a650-490a-47b0-9da9-d4c40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)

https://prod-files-secure.s3.us-west-2.amazonaws.com/6d327 d71-a800-4bb7-a305-2462de4 59e8c/14a91e12-e77e-44f5-8e8 2-6840050bb713/IMG_3266.mo v (https://www.notion.so/signed/https%3A%2F%2Fprod-files-secure.s3.us-west-2.amazonaws.com%2F6d327d71-a800-4bb7-a305-2462de459e8c%2F14a91e12-e77e-44f5-8e82-68400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)

I gave the LED’s their own headers because I wanted to be able to move them around and not have to worry about my already overcomplicated chassis design

int ledR = 20;
int ledG = 19;
int ledB = 18;

void setup() {
pinMode(ledR, OUTPUT);
pinMode(ledG, OUTPUT);
pinMode(ledB, OUTPUT);
}

void loop() {
digitalWrite(ledR, HIGH);
digitalWrite(ledG, HIGH);
analogWrite(ledB, 30); //lower the Blue LED to match intens delay(200);
digitalWrite(ledR, LOW);
digitalWrite(ledG, LOW);
digitalWrite(ledB, LOW);
delay(200);
}

### TCRT5000 Test Code

int TCRT_Left = 26;
int TCRT_Center = 27;
int TCRT_Right = 28;
int TCRT_Output;

void setup() {

Serial.begin(9600);
pinMode(TCRT_Left, INPUT);

pinMode(TCRT_Center, INPUT); pinMode(TCRT_Right, INPUT);
}

// gets reading from TCRT on the right and outputs to serial mon void loop() {
TCRT_Output = analogRead(TCRT_Right);
Serial.print("Right Reading ");
Serial.println(TCRT_Output); delay(500);
}

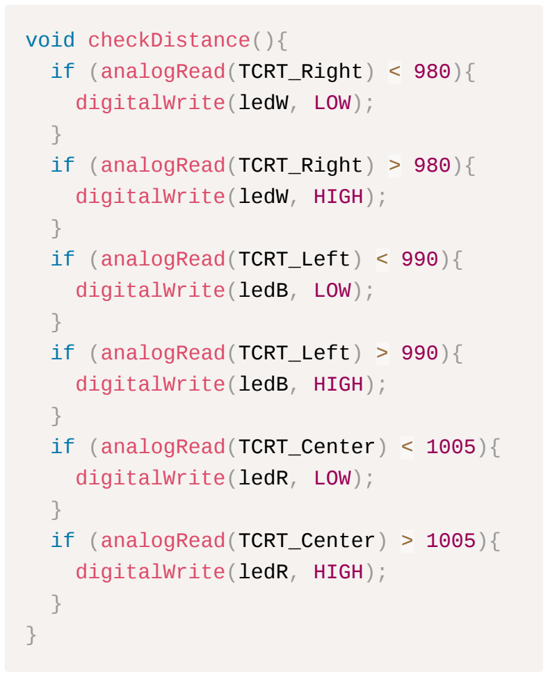
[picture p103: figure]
void checkDistance(){; if (analogRead(TCRT_Right); digitalWrite(ledW, LOW);; digitalWrite(ledW, HIGH);; if (analogRead(TCRT_Left); digitalWrite(ledB, LOW);; digitalWrite(ledB, HIGH);; if (analogRead(TCRT_Center); digitalWrite(ledR, LOW);; digitalWrite(ledR, HIGH);

This basic code was
then updated to trigger
the LED’s when
distance was further
than 8cm with each
sensor. Each sensor is
slightly different which
is shown by the slight
difference in the
readings used to
change the LED’s off
and on.

### Wheel Design - Fusion 360 + Laser Cutter

The wheels went through several iterations as I kept finding problems with each. First off I designed wheels where measurements were exact, but because PLA isnt always perfect they didnt fit on shaft properly. After trying this two or three times I decided to move to laser cutting MDF as it is incredibly fast and less wasteful.

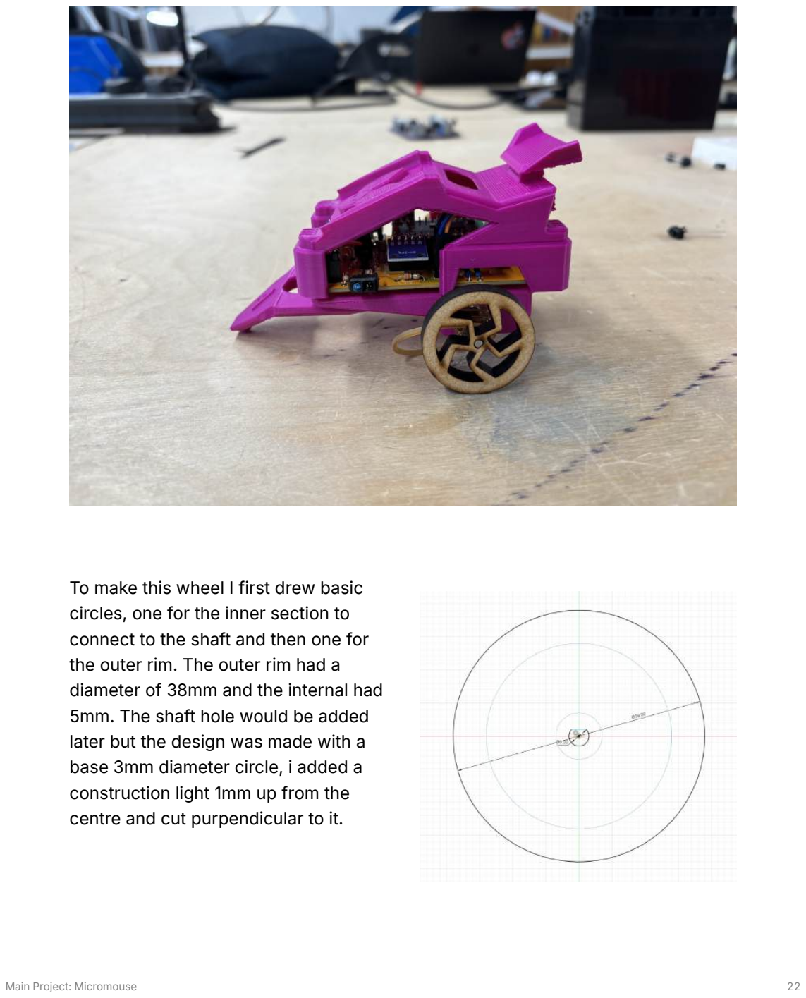
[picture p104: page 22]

To make this wheel I first drew basic circles, one for the inner section to connect to the shaft and then one for the outer rim. The outer rim had a diameter of 38mm and the internal had 5mm. The shaft hole would be added later but the design was made with a base 3mm diameter circle, i added a construction light 1mm up from the centre and cut purpendicular to it.

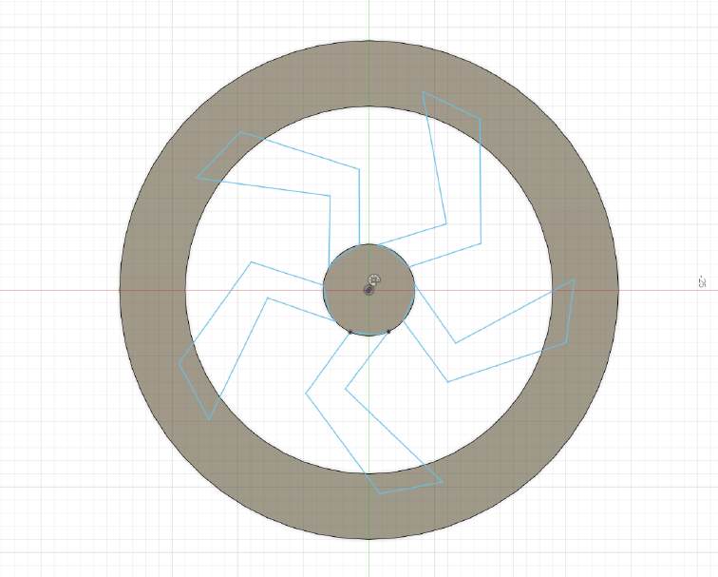
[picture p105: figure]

I then made a single bolt like shape as a wheel spoke and then using the circular pattern feature duplicated it 4 more times around the centre and then extruded through.

This was then exported as a DXF file and laser cut on 6mm MDF.
With it cut I then put all the pieces together and tested with early code

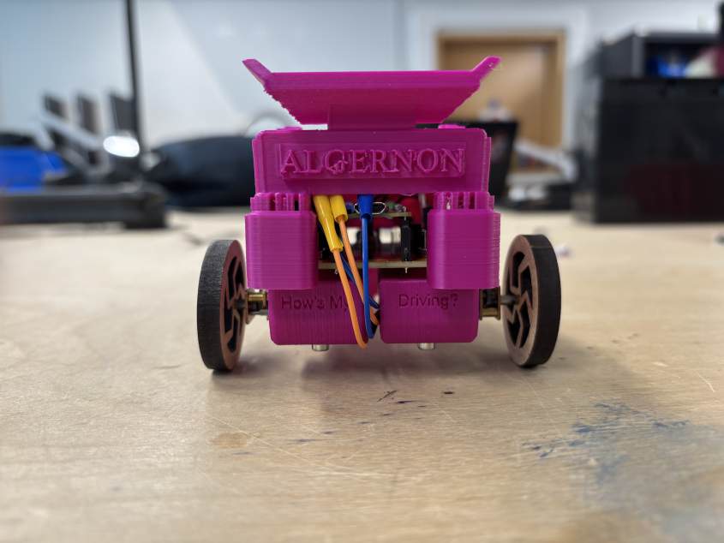
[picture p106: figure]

It was looking good but sadly I felt that it was now too wide. I was advised to not worry about fitting the wheel to the part of the shaft with the cut out section and just make the wheels fit tight. With this information I went to work on what i hoped to be the final design (it was)

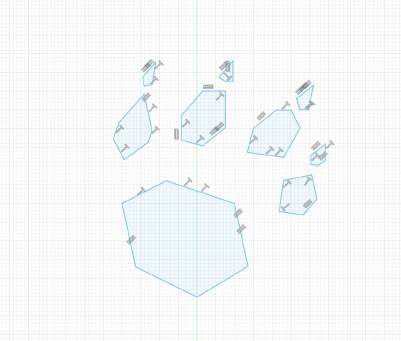
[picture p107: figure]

To make this design I used the same outer diameter but for fun decided to create a crude paw design, this was basic shapes made with the line tool and then using the circular pattern tool rotated it around the centre. I followed this with a rectangle with a filleted corner.

I made the hole just smaller than the shaft so rather than 3mm i made it 2.82mm. this was a snug fit, but to make it extra secure I used hot glue on the outside.

### Third Point Balance - Fusion 360

The third point of balance was created at the same time as the above and then was modified again before the following section.
With the wheels being two points of balance for the micro mouse, so in order for it to keep its balance I designed a small protruding nub that comes from spaces I made on the motor mount.

First i took the measurements from the underside of the motormounts, including their distance apart.

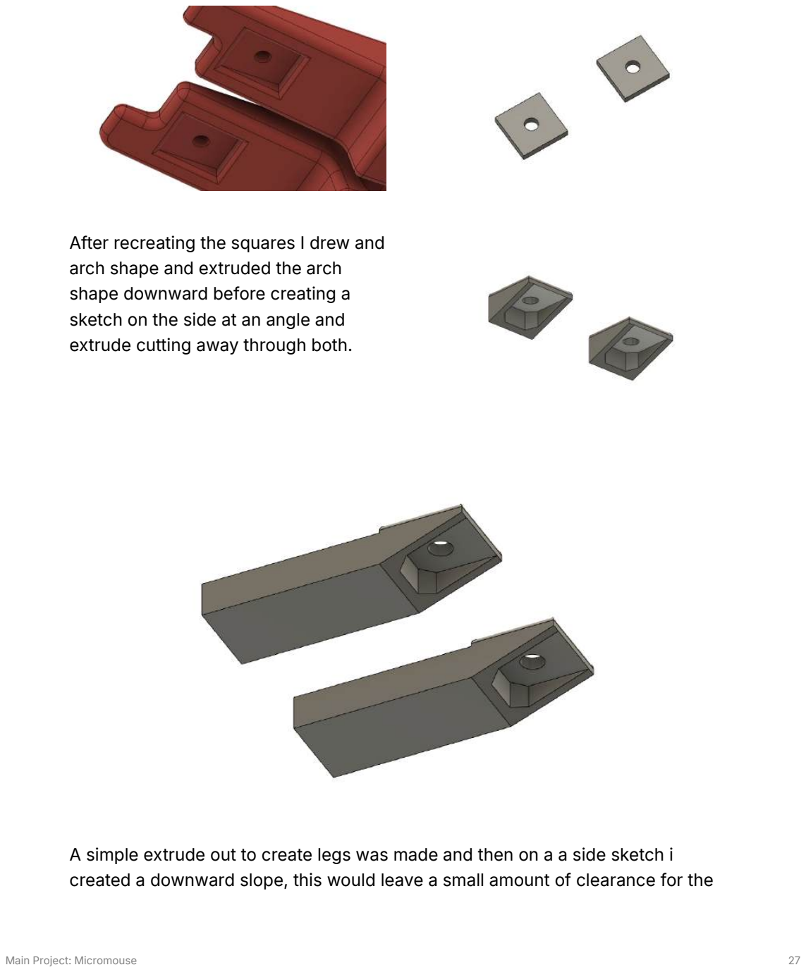
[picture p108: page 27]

After recreating the squares I drew and arch shape and extruded the arch shape downward before creating a sketch on the side at an angle and extrude cutting away through both.

A simple extrude out to create legs was made and then on a a side sketch i created a downward slope, this would leave a small amount of clearance for the nub. The nub was made by cutting a flat square surface on the underside, I did this with a construction plane and a simple extrusion a couple mm deep. From this a 5mm circle was made and then itself extruded. Next I filleted corners and chamfered the longer edges for a nice look.

The above and to the right picture was the original design which worked well but I found it to be too long as the form factor being smaller makes it easier for the mouse to navigate without hitting anything. So I used the split body function to break the legs off from the initial square sections and then extruded the legsback until they hit the curved section before the slop down. Then i simply moved the parts together and used the combine tool to make them one piece again.

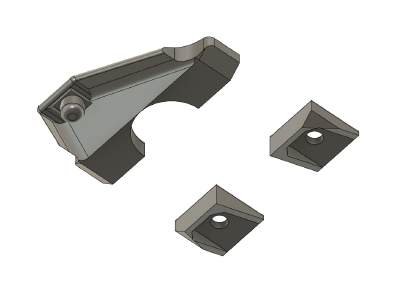
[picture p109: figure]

Added a nice big letter A on the surface and it was good to be attached.

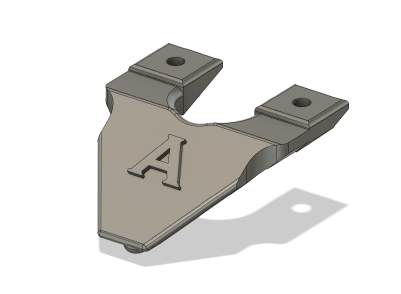
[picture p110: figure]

### Fitting the Compass - Multimeter

The compass was initially easy to fit, I soldered pins to the bottom then attached it to the headers I had already added to the Pi Pico. But there was a problem, I had used the settings mentioned on the sellers page rather than from the data sheet. VCC needed 5v and I had designed the PCB to be 3v. With sage advice from Jamie rather than remaking the whole PCB and other drastic measures i was imagining he said to solder from the top of the Pi Pico (5v pin) directly to the compass.

### Exhaust Pipes - 3D Scanning / Fusion

For the 3D scanning we used a phone app called Polycam. The shape for the exhaust was made out of clay and then scanned with the Polycam application. For best results I took as many photos as it allows to get greater quality. I downloaded the GLTF file and converted it online (just in a brief browser search) to an STL file which I then opened up in fusion

Within Fusion the table had to be
removed, so I created a construction
plane below the 3D image and drew a rectangle larger than said image. Next I extruded upwards. This filled in the hollowness of the underside of the image. From here I drew around the exhaust shape with the spline (from top down view) and then began the painstaking extruding away of the external segments one by one until I was left with just the exhaust. I attempted to extrude away everything outside the splines but it would crash the fusion, I think fusion didnt like the amount of polygons I was trying to intersect at one time.

https://prod-files-secure.s3.us-west-2.amazonaws.com/6d327 d71-a800-4bb7-a305-2462de4 59e8c/2b36841f-8e58-436a-af 10-c23be70ce715/ScreenRecor ding_01-03-2025_12-00-26_1.mo v (https://www.notion.so/signed/https%3A%2F%2Fprod-files-secure.s3.us-west-2.amazonaws.com%2F6d327d71-a800-4bb7-a305-2462de459e8c%2F2b36841f-8e58-436a-af10-c23be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)

Using the mirror tool I easily created the exhausts counterpart

### Battery + Basic Navigation - Arduino IDE

In one of the final workshop sessions we were tasked with breaking down materials in order to retrieve the batteries we then had to attach them to our micro mice to ensure they worked, using our schematics I was able to see which orientation with which to put the wires.

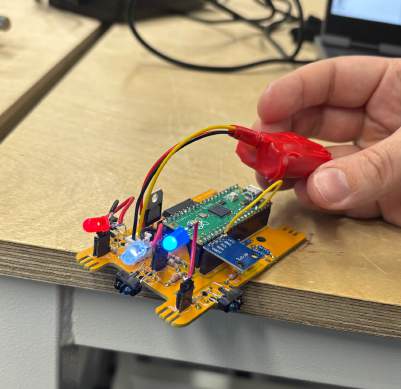
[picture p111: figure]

At this point I had also changed the
middle LED to a plain white one.

Next I put it all together and had the battery hanging off the top, this way I could test some basic code for navigating the maze

Using the below code and some basic
IF statements I was able to get the
mouse to move around, although in a
very clunky manner.

https://prod-files-secure.s3.us-west-2.amazonaws.com/6d327 d71-a800-4bb7-a305-2462de4 59e8c/eef1ebdd-9530-4601-81 90-308ef067bd22/IMG_3484.m ov (https://www.notion.so/signed/https%3A%2F%2Fprod-files-secure.s3.us-west-2.amazonaws.com%2F6d327d71-a800-4bb7-a305-2462de459e8c%2Feef1ebdd-9530-4601-8190-308ef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)

void loop() {

checkTcrt(); // Continuously print sensor readings for debugg

Front | = | false;
Left | = | false;
Right | = | false;

checkDistance();

if (analogRead(TCRT_Front) | < | 950) {
Serial.println("Front sensor triggered");
Front | = | true;

}
if (analogRead(TCRT_Left) | < | 980) {
Serial.println("Left sensor triggered");
Left | = | true;

}
if (analogRead(TCRT_Right) | < | 930) {
Serial.println("Right sensor triggered");
Right | = | true;

}

if (!Front){ | // if nothing detected ahead move forward
motorsForward();
}

else if (!Left){ // if nothing detected to the left turn le turnLeft();
}

else{ | // if neither of the above turn right
turnRight();
}

}

In an attempt to be more specific with my code I actually made things worse so i went back to the code above.

| https://prod-files-secure.s3.us- west-2.amazonaws.com/6d327 d71-a800-4bb7-a305-2462de4 59e8c/59ee77ac-caad-49d1-ad 4a-d02824596e4a/IMG_3482.m ov (https://www.notion.so/signed/https%3A%2F%2Fprod-files-secure.s3.us-west-2.amazonaws.com%2F6d327d71-a800-4bb7-a305-2462de459e8c%2F59ee77ac-caad-49d1-ad4a-d0282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)

### Battery Holder - Fusion 360

With the addition of the battery a final problem was added which was where to place it on the chassis, making it as complicated as I had there was no easy surface to attach it to so i went about designing a battery holder, which i would then incorperate into my chassis design.

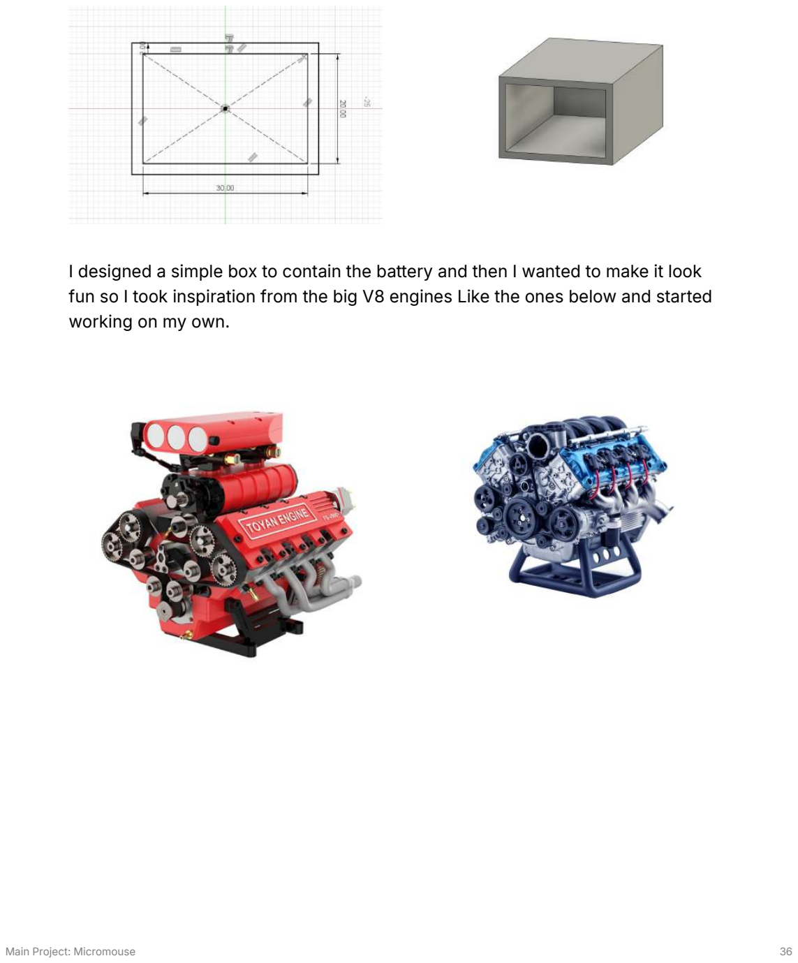
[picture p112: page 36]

I designed a simple box to contain the battery and then I wanted to make it look fun so I took inspiration from the big V8 engines Like the ones below and started working on my own.

Utilising all my prior tools I first created the side angled sections by drawing them on the front sketch then mirroring them and extruding along the body. then to created the ridges I created one thin rectangle, extruded it into the body by 2mm and then use the rectangular pattern function to copy itself 4 more times, using the same procress on the other side to make them match.

The air intake was a simple couple boxes stacked upon the battery, one small and one large. Then I used the shell command to hollow it out. For the face I went back to the chassis design and copied the sketch with the mouse drawing upon it and then pasted it upon the face of the battery (which i angled a little)
The last touch was the tubes, this was new to me but simple ones I had spent some time with it. First I made protruding circles and then used the tube function purpendicular to the protruding circles and made them follow a curved line upwards, this was done twice and then mirrored across to the other side.

### Final Chassis - Fusion 360

In order to incorparate the battery section I had to remove the bonnet and central part of the chassis completely and then add a stanchion closer to the spoiler. This way the wires can easily be connected to the PCB. The only really difficult part here was combining the front of the battery to the paw section containing the LED holders. Because I had overly complicated geometry they initially refused to combine so I had to cut sections away using flat planes in order to connect them.

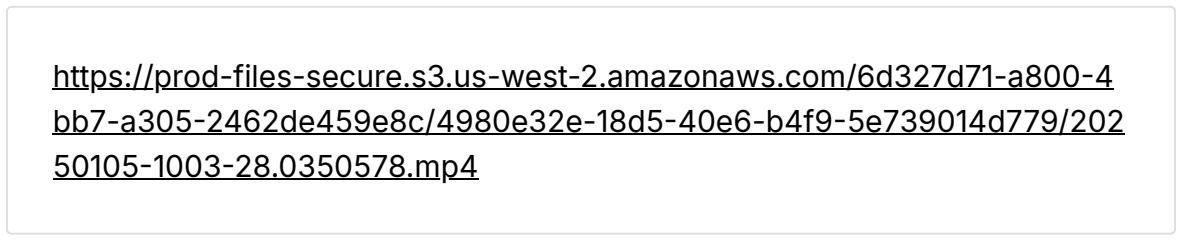
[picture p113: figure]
https://prod-files-secure.s3.us-west-2.amazonaws.com/6d327d71-a800-4 bb7-a305-2462de459e8c/4980e32e-18d5-40e6-b4f9-5e739014d779/202 50105-1003-28.0350578.mp4
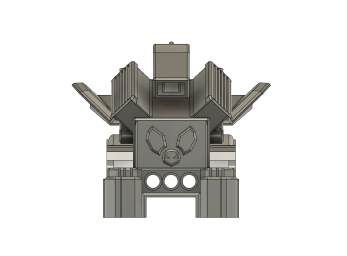
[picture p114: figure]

The final touch I increased the size of the spoiler significantly. To do this I use the scale tool and moved it higher before remaking the stanchion connecting it to the rear.

## Algernon Versus The Maze - Arduino IDE

This simple code helps Algernon traverse the maze, it is a mixture of basic functions reacting to thresholds set to readings from the TCRT's in CM. It currently works at times but is erratic and prone to spinning in place.

// Algernon Current Code

// LED pins
int ledR | = | 20;

int ledW | = | 18;
int ledB | = | 19;

// motor pins
int motor_leftA | = | 0; | // pin0
int motor_leftB | = | 1; | // pin1
int motor_rightB | = | 2; // pin2
int motor_rightA | = | 3; // pin3

// TCRT pins
int TCRT_Left | = | 26;
int TCRT_Front | = | 27;
int TCRT_Right | = | 28;
int TCRT_Output;
bool Front | = | false;
bool Left | = | false;
bool Right | = | false;
int drive_Speed | = | 35;
int turn_Speed | = | 30;
int reverse_Speed | = | 25;
bool firstLoop | = | true;

void setup() {

Serial.begin(9600);

// TCRTS
pinMode(TCRT_Left, OUTPUT); pinMode(TCRT_Front, OUTPUT); pinMode(TCRT_Right, OUTPUT);

// motors
pinMode(motor_leftA, OUTPUT);

pinMode(motor_leftB, OUTPUT); pinMode(motor_rightA, OUTPUT); pinMode(motor_rightB, OUTPUT);

// LEDS
pinMode(ledR, OUTPUT);
pinMode(ledW, OUTPUT);
pinMode(ledB, OUTPUT);
}

void loop() {

if (firstLoop) { // have 4 second delay before starting the l delay(4000);
firstLoop | = | false;
}

checkTcrt(); // Continuously print sensor readings for debugg

Front | = | false; // sensors set to false by deafult so they sta
Left | = | false;
Right | = | false;

checkDistance();

if (analogRead(TCRT_Front) | < | 981) {
Serial.println("Front sensor triggered");
Front | = | true;

}
if (analogRead(TCRT_Left) | < | 995) {
Serial.println("Left sensor triggered");
Left | = | true;

}

if (analogRead(TCRT_Right) | < | 993) {
Serial.println("Right sensor triggered");
Right | = | true;

}

// If all three sensors detect something move backwards
if (Front | && | Left | && | Right){
motorsBackward();
}
else if (Front | && | Left){
turnRight();
}
else if (Front | && | Right){
turnLeft();
}

else if (Left){
turnRight();
}

else if (Right){
turnLeft();
}

else if (Front){
turnLeft();
}

else {
motorsForward();
}
}

// functions
void checkTcrt() {
// 1cm = 543 - 548, 2cm = 851 - 858, 3cm = 940 - 948, // 4cm = 974 - 986, 5cm = 993 - 1002, 6cm = 1002 - 1023, // 7cm = 1007 - 1015, 8cm = 1008 - 1018
Serial.print(" Right Reading "); Serial.print(analogRead(TCRT_Right));

// 1cm = 567 - 569, 2cm = 869 - 876, 3cm = 950 - 959, // 4cm = 980 - 990, 5cm = 995 - 1005, 6cm = 1003 - 1013, // 7cm = 1010 - 1018, 8cm = 1013 - 1021 Serial.print("| Left Reading "); Serial.print(analogRead(TCRT_Left));

// 1cm = 691 - 700, 2cm = 892 - 898, 3cm 953 - 964, // 4cm = 981 - 990, 5cm = 994 - 1003, 6cm 1001 - 1011, // 7cm = 1007 - 1015, 8cm = 1007 - 1019 Serial.print("| Center Reading "); Serial.println(analogRead(TCRT_Front));
delay(500);
}

void checkDistance() {
if (analogRead(TCRT_Right) | < | 980) {
digitalWrite(ledW, LOW);
}
if (analogRead(TCRT_Right) | > | 980) {
digitalWrite(ledW, HIGH);
}
if (analogRead(TCRT_Left) | < | 990) {
digitalWrite(ledB, LOW);
}
if (analogRead(TCRT_Left) | > | 990) {
digitalWrite(ledB, HIGH);
}

if (analogRead(TCRT_Front) | < | 1005) {
digitalWrite(ledR, LOW);
}
if (analogRead(TCRT_Front) | > | 1005) {
digitalWrite(ledR, HIGH);
}
}

void turnLeft() {
analogWrite(motor_leftA, -turn_Speed); analogWrite(motor_leftB, turn_Speed); analogWrite(motor_rightA, turn_Speed); analogWrite(motor_rightB, -turn_Speed); }

void turnRight() {
analogWrite(motor_leftA, turn_Speed);
analogWrite(motor_leftB, | -turn_Speed);
analogWrite(motor_rightA, | -turn_Speed);
analogWrite(motor_rightB, turn_Speed); }

void motorsForward() {

analogWrite(motor_leftA, drive_Speed); analogWrite(motor_leftB, -drive_Speed); analogWrite(motor_rightA, drive_Speed); analogWrite(motor_rightB, -drive_Speed);

}

void motorsBackward() {
analogWrite(motor_leftA, | -reverse_Speed); // Reverse left mot
analogWrite(motor_leftB, reverse_Speed); | // Reverse left mot
analogWrite(motor_rightA, | -reverse_Speed); // Reverse right mo
analogWrite(motor_rightB, reverse_Speed); // Reverse right mo

}

void allLeds() {
digitalWrite(ledR, HIGH);
digitalWrite(ledW, HIGH);
digitalWrite(ledB, HIGH);
}

### Final additions - Fusion 360

When attempting the maze I found two issues to be solved firstly the MDF had a hard time gripping the ground and seconding the wheels were getting caught when going around a hairpin turn.

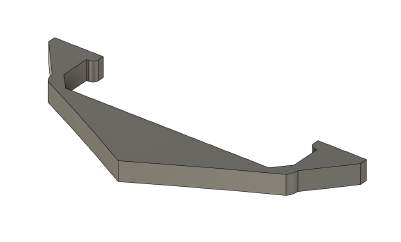
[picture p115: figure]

For the latter I designed a bumber that
simply clips onto the front of the mouse. To make this I took measurement around the front and simply drew an arrow shape with hooks on the side and then extruded the pattern.

Placing this bumper at the front helps the thin walls not get caught between the chassis and the wheels.

For the Wheels I made a circle the same diameter as the wheels 38mm and then offset this by 1mm and extrudes the width of the MDF which was 6mm. I then offset the larger circle again on either side and extruded inwards by 2mm. Then I decided to make it so the tire couldnt slide off the wheel by making a third offset, but this one would be a smaller circle effectively making them like caps on the wheels. Then the outer edge was filleted.

https://prod-files-secure.s3.us-west-2.amazonaws.com/6d327 d71-a800-4bb7-a305-2462de4 59e8c/3091c0d4-9f88-4465-8 7fe-123d1ec6af40/20250106-17 45-28.3511821.mp4 (https://www.notion.so/signed/https%3A%2F%2Fprod-files-secure.s3.us-west-2.amazonaws.com%2F6d327d71-a800-4bb7-a305-2462de459e8c%2F3091c0d4-9f88-4465-87fe-123d1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)

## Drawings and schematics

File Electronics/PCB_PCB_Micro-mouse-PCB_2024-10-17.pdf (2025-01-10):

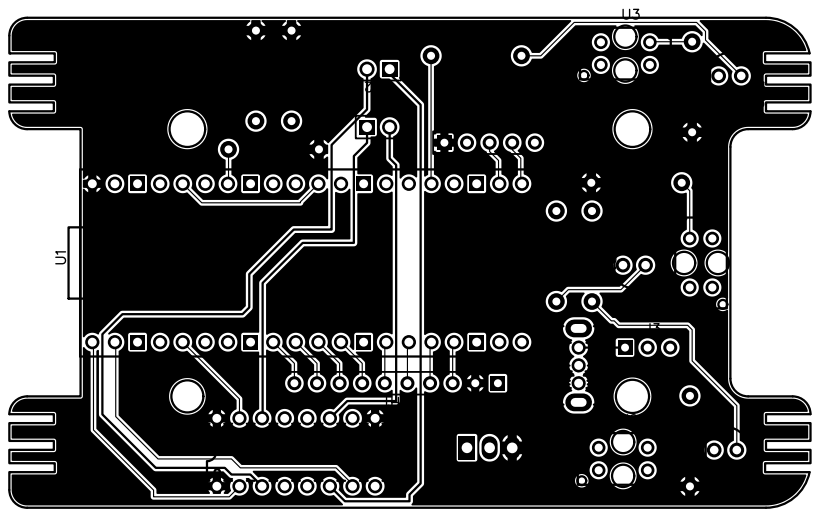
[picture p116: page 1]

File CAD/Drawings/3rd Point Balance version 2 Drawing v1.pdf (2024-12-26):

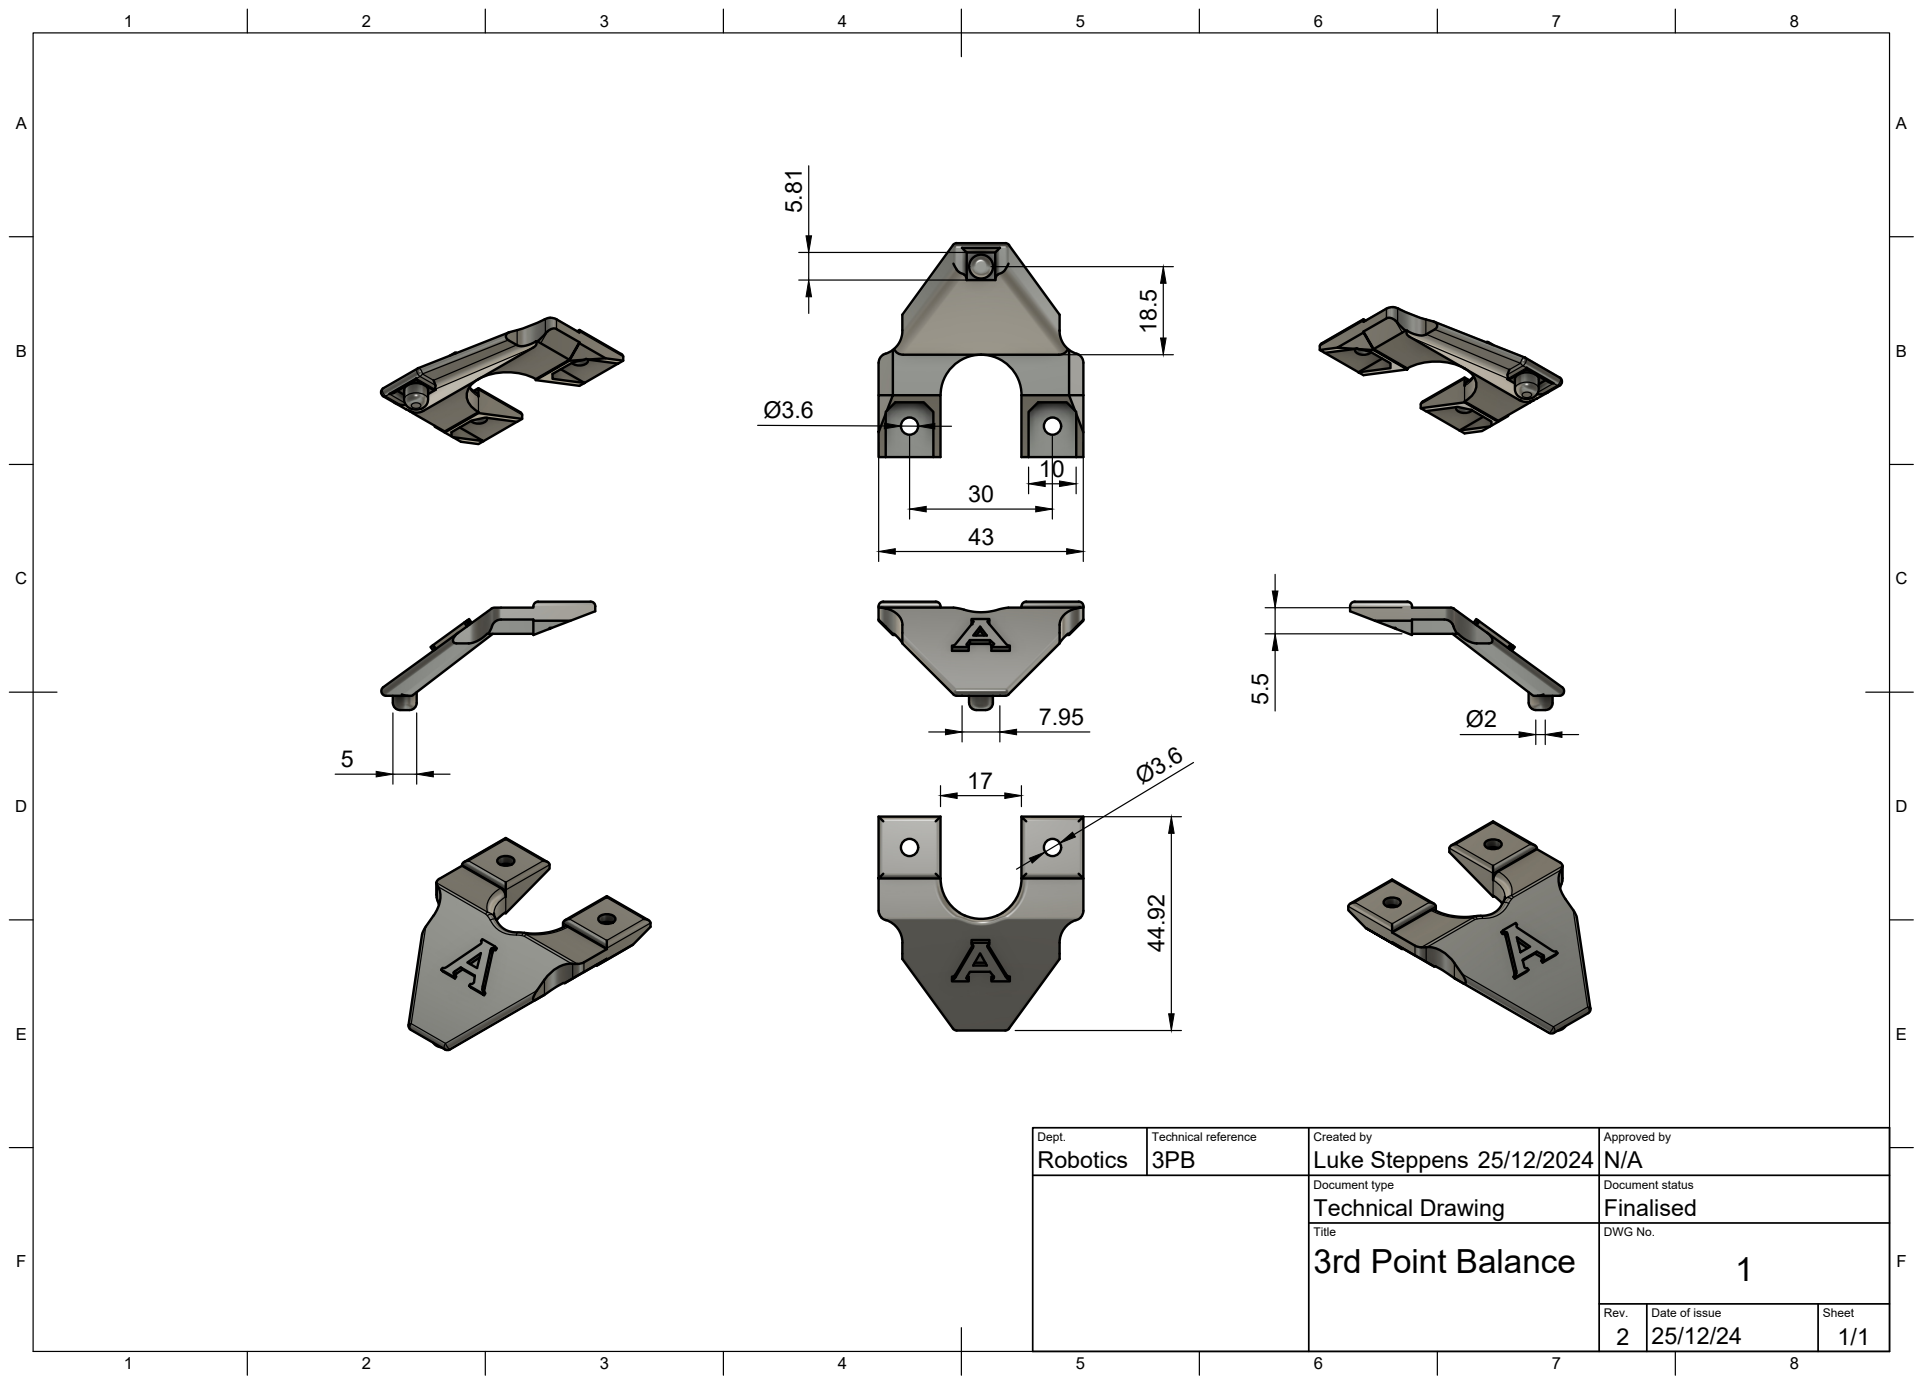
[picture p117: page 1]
Title; DWG No.; Rev.; Date of issue; Sheet; 3rd Point Balance

Dept. Robotics | Technical reference 3PB | Created by Luke Steppens 25/12/2024 | Approved by N/A

Document type Technical Drawing | Document status Finalised

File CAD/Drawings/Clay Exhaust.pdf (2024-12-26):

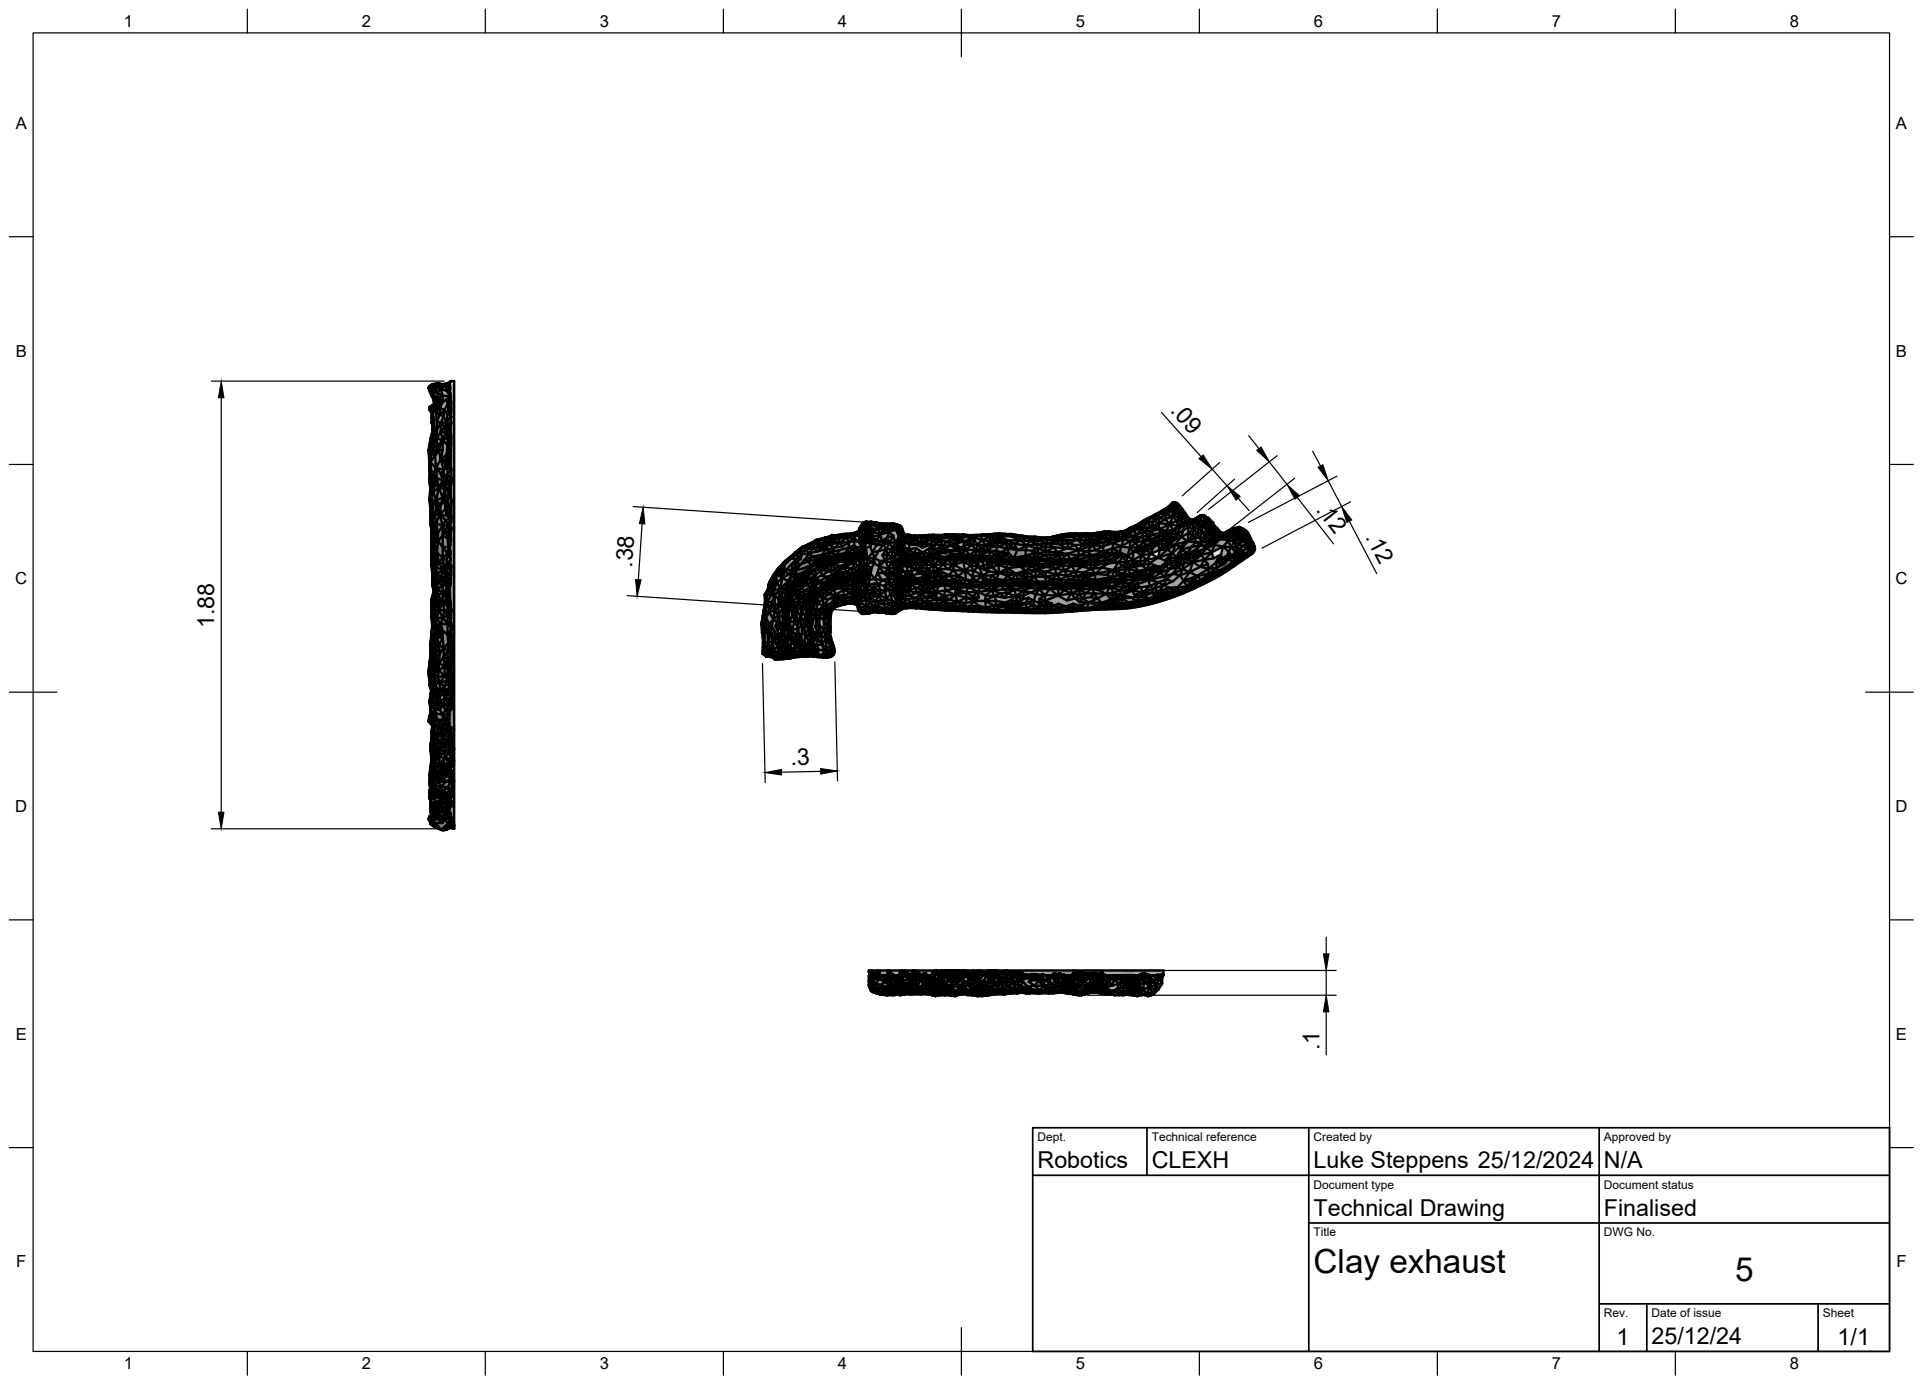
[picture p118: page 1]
Dept.; Technical reference; Created by; Approved by; Document type; Document status; Title; DWG No.; Rev.; Date of issue; Sheet; Technical Drawing; Finalised; Clay exhaust; Robotics CLEXH; Luke Steppens

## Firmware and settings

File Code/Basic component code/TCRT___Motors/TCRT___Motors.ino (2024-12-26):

int ledR = 20;
int ledG = 19;
int ledB = 18;

// Motor Pins
int motor_leftA = 0;   // pin0
int motor_leftB = 1;   // pin1

int motor_rightA = 2;  // pin2
int motor_rightB = 3;  // pin3

int TCRT_Left = 26;
int TCRT_Center = 27;
int TCRT_Right = 28;
int TCRT_Output;


void setup() {

  Serial.begin(9600);
  pinMode(TCRT_Left, INPUT);
  pinMode(TCRT_Center, INPUT);
  pinMode(TCRT_Right, INPUT);
  
  pinMode(motor_leftA, OUTPUT);
  pinMode(motor_leftB, OUTPUT);
  pinMode(motor_rightA, OUTPUT);
  pinMode(motor_rightB, OUTPUT);
}

void loop() {
  TCRT_Output = analogRead(TCRT_Right);
  Serial.print("Right Reading ");
  Serial.println(TCRT_Output);
  delay(500);
  digitalWrite(motor_leftA, HIGH);
  digitalWrite(motor_leftB, LOW);
}

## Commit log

2024-12-26 Feat: Copy from uni account
    copied across from university account
    [3rd Point Balance v16.stl, 3rd Point Balance version 2 v2.f3d, Arcade cabinet v4.stl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]
2025-01-10 feat: duplicate items from uni git
    mass movement of items to be resorted for personal use
    [Arcade cabinet v4.stl, Assembly test v15.stl]
